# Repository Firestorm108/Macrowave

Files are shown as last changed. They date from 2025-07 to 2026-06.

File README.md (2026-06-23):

# Macrowave



A smart annealing system for 3D printed functional parts! It utilizes heating features such as a heated aluminum bed and infared heating lights that allow it to get up to 80C, perfect for PLA and PETG! My 3D printed parts
aren't always strong enough for my use cases, and I didn't want to ruin my oven by sticking my parts in there. So, I designed a cool looking annealing system that would do it better! Annealing is very effective, it can do crazy things like increase the heat resistance of PLA to 100C. It utilizes a rotating bed to evenly distribute the heat. Whatever 3D printed part you can fit on the plate, it'll easily be able to move it! Overall, it'll be an amazing machine to use for all kinds of projects in the future, and was a really fun project in itself!

<h1>What is annealing?</h1>

Annealing is the process of heating something in a controlled way and cooling it in a controlled way in order to relieve stress and increase properties of the object. It's used with all kinds of materials, from metals to plastics and more!

<h1>Pictures</h1>

Assembly v40

CleanShot 2025-07-06 at 13 49 01

CleanShot 2025-07-06 at 13 48 49

<h1>The BOM</h1>
Bill of Materials

| Category | Item | Price  |
|---|---|---|
| Frame | Regular ASA  *(Already Owned)* | $0 |
| | Reflective Insulation Panels | $0 |
| | [12mm x 305mm Steel Rods](https://www.amazon.com/uxcell-Stainless-Steel-305mm-Working/dp/B0DKXSZ9M8/)  | $17 |
| | [150mm Aluminum Disc](https://www.amazon.com/uxcell-Aluminum-Diameter-Thickness-Stamping/dp/B0DQ8H1FZG/) | $7 |
| Control | [12V → 5V Buck Converter](https://www.aliexpress.us/item/3256808220206305.html) | $4 |
| | [Raspberry Pi Pico (Surface Mount)](https://www.aliexpress.us/item/3256806910537897.html) | $4 |
| | [2.8" Touch Display](https://www.aliexpress.us/item/3256806437054690.html) | $6 |
| | [Toggle Switch SPDT](https://www.aliexpress.us/item/2251832806771133.html) | $2 |
| Mains Power | [Mains Plug](https://www.aliexpress.us/item/3256805500507047.html) | $6 |
| | [Fuses](https://www.aliexpress.us/item/3256806781121800.html) | $3 |
| | [Connector Plug Socket](https://www.aliexpress.us/item/2251832520633643.html) | $2 |
| | [12 AWG Wire](https://www.aliexpress.us/item/3256807619400327.html) | $4 |
| Bed Movement | [12V 10A Power Supply](https://www.amazon.com/Universal-Regulated-Switching-Industrial-Transformer/dp/B0CCL86TGY/) | $16 |
| | [5V 1-Channel Relay](https://www.aliexpress.us/item/3256805679282465.html) | $4 |
| | [10RPM 12V Brushed DC Motor](https://www.aliexpress.us/item/2251832801627453.html) | $10 |
| | [Slip Ring 2 Channels 5A](https://www.aliexpress.us/item/2251832799374262.html) | $14 |
| Bed Heating | [150mm Circular Heating Pad](https://www.aliexpress.us/item/3256805151930305.html) | $18 |
| | [40A SSR](https://www.aliexpress.us/item/2251832734722079.html) | $4 |
| | [DS18B20 Temperature Probe](https://www.aliexpress.us/item/3256807353480124.html) | $3 |
| Infrared Light Heating | [Infrared Light Bulbs](https://www.amazon.com/REPTI-ZOO-Infrared-Reptile-Emitter/dp/B0B5W8XCNH/)  | $18 |
| | [40A SSR](https://www.aliexpress.us/item/2251832734722079.html) | $4 |
| | [DS18B20 Temperature Probe](https://www.aliexpress.us/item/3256807353480124.html) | $3 |
| | [E26 Light Sockets](https://www.amazon.com/Ceramic-Standard-Medimun-Halogen-Incandescent/dp/B07FMRLSWC/) | $10 |
| | [Socket Extender/Twisters](https://www.amazon.com/DiCUNO-Extension-All-Directional-Adjustable-Converter/dp/B078WJJ7VZ/) | $8 |
| Cooling | [BLDC 12V Cooling Fan (12025 12V Dual Ball IP67)](https://www.aliexpress.us/item/3256807400971120.html) | $8 |
| | [5V 1-Channel Relay](https://www.aliexpress.us/item/3256805679282465.html) | $4 |
| JLCPCB | PCB *(w/ shipping)* | $5.30  |
| Screws | 10-30mm M4, M3, M5 Screws *(Already Owned)* | $0 |
| | | |
| **Total** | | **$182.30** |

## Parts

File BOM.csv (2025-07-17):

Frame:
Regular ASA/ABS - $0 (Already Owned)
12mm Diameter x 305mm Height Metal Rods - $17 (https://www.amazon.com/uxcell-Stainless-Steel-305mm-Working/dp/B0DKXSZ9M8/)
150mm Aluminum Disc - $7 (https://www.amazon.com/uxcell-Aluminum-Diameter-Thickness-Stamping/dp/B0DQ8H1FZG/)
Reflective Insulation Panels -  $0 (Already Owned)
Control:
12V -> 5V Buck Converter - $4 (https://www.aliexpress.us/item/3256808220206305.html)
Raspberry Pi Pico (Surface Mount) - $4 (https://www.aliexpress.us/item/3256806910537897.html)
2.8 Inch Touch Display - $6 (https://www.aliexpress.us/item/3256806437054690.html)
Toggle Switch - $2 (https://www.aliexpress.us/item/2251832806771133.html)
Mains Power:
Mains Plug - $6 (https://www.aliexpress.us/item/3256805500507047.html)
Fuses - $3 (https://www.aliexpress.us/item/3256806781121800.html)
Connector Plug Socket - $2 (https://www.aliexpress.us/item/2251832520633643.html)
12 AWG Wire - $4 (https://www.aliexpress.us/item/3256807619400327.html)
Bed Movement:
12V 10A Power Supply - $16 (https://www.amazon.com/Universal-Regulated-Switching-Industrial-Transformer/dp/B0CCL86TGY/)
5V 1 Channel Relay - $4 (https://www.aliexpress.us/item/3256805679282465.html)
10RPM 12V Brushed DC Motor - $10 (https://www.aliexpress.us/item/2251832801627453.html)
Slip Ring 2 Channels 5A - $14 (https://www.aliexpress.us/item/2251832799374262.html)
Bed Heating:
150mm D Circular Heating Pad - $18 (https://www.aliexpress.us/item/3256805151930305.html)
40A SSR - $4 (https://www.aliexpress.us/item/2251832734722079.html)
DS18B20 Temperature Probe - $3 (https://www.aliexpress.us/item/3256807353480124.html)
Infrared Light Heating:
Infrared Light Bulbs - $18 (https://www.amazon.com/REPTI-ZOO-Infrared-Reptile-Emitter/dp/B0B5W8XCNH/)
40A SSR - $4 (https://www.aliexpress.us/item/2251832734722079.html)
DS18B20 Temperature Probe - $3 (https://www.aliexpress.us/item/3256807353480124.html)
E26 Light Sockets - $10 (https://www.amazon.com/Ceramic-Standard-Medimun-Halogen-Incandescent/dp/B07FMRLSWC/)
Socket Extender/Twisters - $8 (https://www.amazon.com/DiCUNO-Extension-All-Directional-Adjustable-Converter/dp/B078WJJ7VZ/)
Cooling:
BLDC 12V Cooling Fan (12025 12V Dual Ball IP67) - $8 (https://www.aliexpress.us/item/3256807400971120.html)
5V 1 Channel Relay - $4 (https://www.aliexpress.us/item/3256805679282465.html)
JLCPCB:
PCB - $5.30
Screws:
10-30mm M4 Screws (Already Owned)
10-30mm M3 Screws (Already Owned)
10-30mm M5 Screws (Already Owned)
Total Price: $182.30

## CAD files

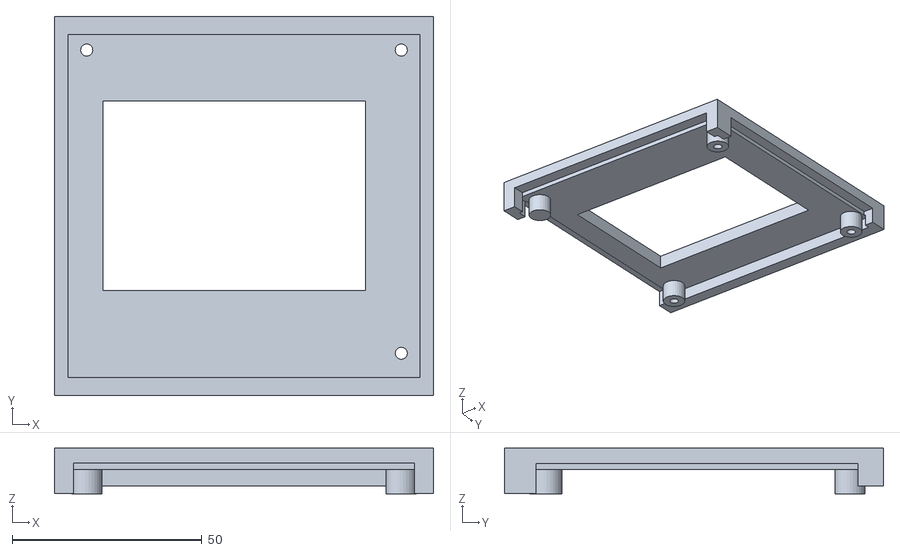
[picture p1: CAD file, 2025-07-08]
Macrowave Print Files/PCB Cover.stl
100.0 x 100.0 x 12.1

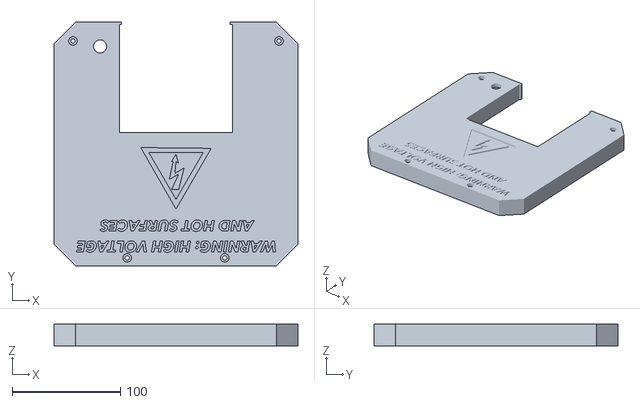
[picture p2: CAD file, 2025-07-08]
Macrowave Print Files/Lid.stl
225.0 x 225.0 x 20.0

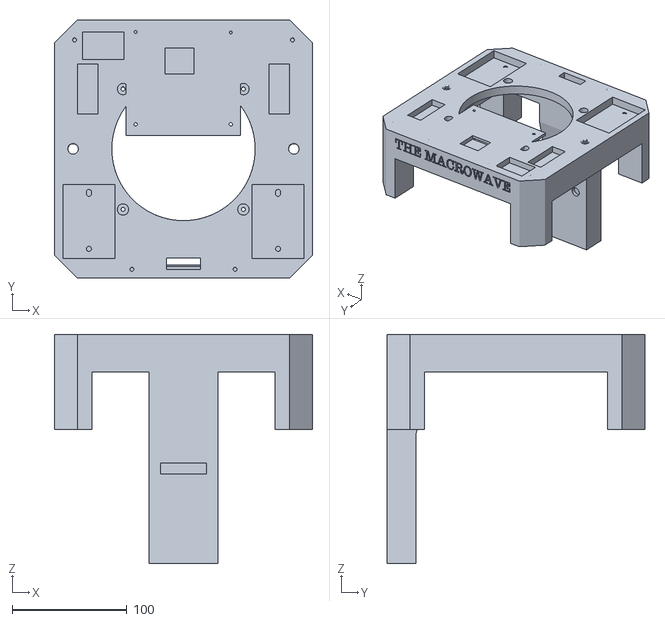
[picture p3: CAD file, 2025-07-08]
Macrowave Print Files/Top.stl
225.0 x 225.0 x 200.0

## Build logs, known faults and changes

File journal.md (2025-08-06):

<h1>Summary</h1>
The MacroWave is an annealing machine that evenly heats up 3D printed parts and cools them down to strenghten them! Similar to a microwave, it emits macro wavelengths of light (even though microwaves emit LONGER waves than the macrowave- isn't that funny?).

<h1>25 Hours Total</h1>

<h1>July 4th</h1>
Today I made a BOM with an overall thought process of the design of the machine. It's got features like an easy to use touch screen, 4 bulbs, a heating pad, PWM control, sensors, and a rotating bed!



Total Time Spent: 3 Hours

<h1>July 5th</h1>
After some changes to the design and BOM-optimizing (like switching 4 bulbs into 2 higher wattage bulbs), I began work on the PCB. I ended up finishing the entire PCB and squeezed it into less than 100mmx100mm so it should be able to fit in the budget. The PCB is just for the main control area and linking up all the components since a lot of the components aren't supposed to be mounted to the PCB.
Seeing the beautiful green "0 errors" in the DRC was the best part of all of this.

CleanShot 2025-07-05 at 15 27 45

After that, I began work on the CAD. This took me the entire day, I'm writing this as of now when I've finished (without adding materials and colors and renders) at 12:27 AM after working the whole day. I'm really proud of how it came out. So first, I did the bottom. This consisted of a heated bed with an aluminum plate on top that is spun by a gearbox motor. I made the gear ratio so that the 10RPM would be converted to 5RPM due to annealing being a slow process.

CleanShot 2025-07-06 at 00 28 43

CleanShot 2025-07-06 at 00 28 32

After that, I worked on the mains wiring as well as the 12V and 5V power. I added a sturdy structural system as well as the lights themselves. The entire top part was done as well which has a nice, large cooling fan, housing for the PCB and relays, areas to route the wires, and a cool design!

CleanShot 2025-07-06 at 00 29 46

CleanShot 2025-07-06 at 00 30 04

CleanShot 2025-07-06 at 00 30 28

CleanShot 2025-07-06 at 00 30 42

Total Time Spent: 17 Hours (im going to sleep now)

<h1>July 6th</h1>

This morning, I started off by changing materials and getting some nice renders of the CAD. I really like how nice it looks, and I chose red (white would be good too) due to it reflecting the red light back to the plate.

Assembly v38 5
Assembly v38 4
Assembly v38 3
Assembly v38 2
Assembly v38

After that, I finished the wiring diagram!

CleanShot 2025-07-06 at 10 53 06

I then finalized my README, BOM, uploaded my files, double checked prices, etc. It all looks good, I should be paying ~$30 out of pocket at the most optimized BOM.

Updated the wiring diagram as well to add a switch for better control instead of touch. I also updated the CAD.

CleanShot 2025-07-06 at 12 40 23

CleanShot 2025-07-06 at 12 40 57

After that, I attempted to get the firmware going, which took WAY longer than expected especially due to the touchscreen, but all the basic logic is there. If it doesn't work it'll probably just be a couple small changes since I don't actually have the physical screen and other components right now to test. Overall, everything should be ready to be built now.

Total Time Spent: ~5 Hours

<h1>August 3rd</h1>

I printed all the parts last night and got them together. My PCB however cannot be used, sadly because the microcontroller got bricked on arrival. There is no time to order another, so I'll be using a spare esp32 I found in my closet (luckily). I spent a good 2 hours trying to desolder the screen but in the end I had to break off the header pins. My whole room was in a fog of flux. After that, I wired up the power supply and mains AC input connector which worked great surprisingly! I have to say it was scary plugging it into the wall but when the led light on the switch lit up that was a good feeling. Anyways, the gearbox motor that spins the bed was not connected to the 3d printed gear super well. So I used my heat gun to have it shape to the shaft really well, which allowed it to spin over 5lbs of weight! (i didn't test any higher). 






Time Spent: 6 Hours

<h1>August 4th</h1>

Today started out well. I finished all the mains wiring and it all worked! However, the TFT display came broken and thus I had to think of a different way to provide feedback to the user. An LCD Display would've been good, but my only one doesn't use I^2C and so I'd have to connect like 15 pins which is just absurd. I don't have any other displays on me, so the only rational answer is to redesign the small pcb cover on the top to accomodate a few indicator LEDs. Such as, the material selection could have 2, heating, power, etc. I think that this will still work well.





Watching B99 while working on this the whole day was pretty fun too

Time Spent: 12 Hours

<h1>August 5th</h1>

I finished the project! I added the LEDs to indicate stuff, the code, and cleaned up the wiring! Not much else to say, but here's some pictures :)





Time Spent: 8 Hours

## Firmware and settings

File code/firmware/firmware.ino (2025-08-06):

#include <Adafruit_NeoPixel.h>

#define PLA_PIN     5    
#define PETG_PIN    17  

#define BULB_PIN    14   
#define FAN_PIN     26    
#define MOTOR_PIN   4    
#define BED_PIN     27   

#define LED_PIN     13    
#define NUMPIXELS   8   

Adafruit_NeoPixel pixels(NUMPIXELS, LED_PIN, NEO_GRB + NEO_KHZ800);

unsigned long previousMillis = 0;
int bedInterval = 0;
bool bedState = false;

void setup() {
  pinMode(PLA_PIN, INPUT_PULLUP);
  pinMode(PETG_PIN, INPUT_PULLUP);

  pinMode(BULB_PIN, OUTPUT);
  pinMode(FAN_PIN, OUTPUT);
  pinMode(MOTOR_PIN, OUTPUT);
  pinMode(BED_PIN, OUTPUT);

  digitalWrite(BULB_PIN, LOW);
  digitalWrite(FAN_PIN, LOW);
  digitalWrite(MOTOR_PIN, LOW);
  digitalWrite(BED_PIN, LOW);

  pixels.begin();
  pixels.show(); 
}

void loop() {
  bool plaMode = digitalRead(PLA_PIN) == LOW;
  bool petgMode = digitalRead(PETG_PIN) == LOW;

  if (plaMode && !petgMode) {
    digitalWrite(BULB_PIN, HIGH);
    digitalWrite(FAN_PIN, HIGH);
    digitalWrite(MOTOR_PIN, HIGH);
    bedInterval = 15000;

    setAllPixels(pixels.Color(0, 0, 255));

    handleBedInterval(bedInterval);

  } else if (petgMode && !plaMode) {
    digitalWrite(BULB_PIN, HIGH);
    digitalWrite(FAN_PIN, HIGH);
    digitalWrite(MOTOR_PIN, HIGH);
    bedInterval = 10000;


    setAllPixels(pixels.Color(255, 165, 0));

    handleBedInterval(bedInterval);

  } else {

    digitalWrite(BULB_PIN, LOW);
    digitalWrite(FAN_PIN, LOW);
    digitalWrite(MOTOR_PIN, LOW);
    digitalWrite(BED_PIN, LOW);
    bedState = false;


    rainbowCycle(2);
  }
}

void setAllPixels(uint32_t c) {
  for (int i = 0; i < NUMPIXELS; i++) {
    pixels.setPixelColor(i, c);
  }
  pixels.show();
}


void handleBedInterval(int interval) {
  unsigned long currentMillis = millis();
  if (currentMillis - previousMillis >= interval) {
    previousMillis = currentMillis;
    bedState = !bedState;
    digitalWrite(BED_PIN, bedState ? HIGH : LOW);
  }
}

void rainbowCycle(uint8_t wait) {
  static uint16_t j = 0;
  for (int i = 0; i < NUMPIXELS; i++) {
    pixels.setPixelColor(i, Wheel((i * 256 / NUMPIXELS + j) & 255));
  }
  pixels.show();
  j++;
  delay(wait);
}


uint32_t Wheel(byte WheelPos) {
  WheelPos = 255 - WheelPos;
  if (WheelPos < 85) {
    return pixels.Color(255 - WheelPos * 3, 0, WheelPos * 3);
  } else if (WheelPos < 170) {
    WheelPos -= 85;
    return pixels.Color(0, WheelPos * 3, 255 - WheelPos * 3);
  } else {
    WheelPos -= 170;
    return pixels.Color(WheelPos * 3, 255 - WheelPos * 3, 0);
  }
}

                                                                                       

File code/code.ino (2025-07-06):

#include <Adafruit_GFX.h>
#include <Adafruit_ILI9341.h>

#define TFT_CS 7  
#define TFT_RST 8
#define TFT_DC 9
#define TFT_MOSI 3
#define TFT_SCK 2
#define TFT_LED 12
#define TFT_MISO 0

String material = "plastic";

Adafruit_ILI9341 tft = Adafruit_ILI9341(TFT_CS, TFT_DC, TFT_RST);

void setup() {
  Serial.begin(115200);
  tft.begin();
  tft.fillScreen(ILI9341_BLACK);
  tft.setTextColor(ILI9341_WHITE);
  tft.setTextSize(3);
  tft.setCursor(50, 50);
  tft.print("Initializing!!!");
  delay(5000);
  tft.fillScreen(ILI9341_BLACK);
  tft.setCursor(0, 50);
  tft.print("PLA");
  tft.setCursor(50, 50);
  tft.print("PETG");
  delay(5000);

  digitalWrite(10, HIGH);

  bool switchIsOn = digitalRead(16) == LOW;

  if (switchIsOn) {
    Serial.println("digitalRead(TOGGLE_SWITCH_PIN) == LOW");
    tft.fillScreen(ILI9341_BLACK);
    tft.setCursor(50, 50);
    material = "PLA";
    PWM(material);
    tft.print("Setting up for PLA");
  } else {
    tft.fillScreen(ILI9341_BLACK);
    tft.setCursor(50, 50);
    material = "PETG";
    PWM(material);
    tft.print("Setting up for PETG");
  }
}

void END() {
  digitalWrite(5, LOW);
  digitalWrite(6, LOW);
  digitalWrite(1, HIGH);
  digitalWrite(10, LOW);

  delay(30000);
  digitalWrite(1, LOW);
}

void PWM(String material) {
  pinMode(5, OUTPUT);
  pinMode(6, OUTPUT);
  pinMode(11, INPUT_PULLUP);
  pinMode(4, INPUT_PULLUP);
  analogWriteFreq(1000);
  analogWrite(5, 0);
  analogWrite(6, 0);
  int targetTempC = 0;
  if (material == "PLA") {
    targetTempC = 60;
  } else if (material == "PETG") {
    targetTempC = 80;
  }
  tft.fillScreen(ILI9341_BLACK);
  tft.setCursor(50, 50);
  int time = 60;
  while (time > 0) {
    delay(60000);
    time = time - 1;
    if (time == 0) {
      END();
    }
  }
}

void loop() {
  int probe1State = digitalRead(11);
  int probe2State = digitalRead(4);
  int pwm1 = (probe1State == LOW) ? 255 : 0;
  int pwm2 = (probe2State == LOW) ? 255 : 0;
  analogWrite(5, pwm1);
  analogWrite(6, pwm2);
}

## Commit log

2025-07-06 Create Assembly v39.step
2025-07-06 changed CAD files updated
2025-08-06 Create Assembly v45.step
